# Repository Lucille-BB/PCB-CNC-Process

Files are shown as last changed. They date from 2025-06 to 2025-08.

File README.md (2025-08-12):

# PCB Creation - 3018 Genmitsu CNC

## Purpose
This is documentation from UW-Milwaukee - Center for Sustainable Electrical Energy Systems (SEES) and Microgrid Storage - in order to provide a (somewhat) step by step process for making in house PCB's. 

The PCB in this documentation is very simple. We are integrating NI Modules into the cabinets that control the Microgrid, that read current and voltage sensors. All the PCB is doing is running the NI module and sensor on one end across a 100* ohm resistor, and into two 15 VDC converters. So, we have 20 2-pin connectors and 10 resistors. 

Moreover, I will be providing some of the errors I made in this process to avoid repetitive mistakes, design errors, and unusable boards. Expect to make multiple iterations or redo some parts. I have had to go back and forth in the design process many times to understand the machine and the software. 

## Version History
Similar to the [Severson Group](https://github.com/Severson-Group), the Altium Files for this PCB are saved in this repository as **Vermmddyyyy**

## Software
-------

## Process
* [Altium](./altium.md)
* [FlatCam](./flatcam.md)
* [Candle](./Grbl_candle.md)
* [Outside Resources](./resourcesandlinks.md)

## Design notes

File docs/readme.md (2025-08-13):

# PCB Creation - 3018 Genmitsu CNC

## Purpose
This is documentation from UW-Milwaukee - Center for Sustainable Electrical Energy Systems (SEES) and Microgrid Storage - in order to provide a (somewhat) step by step process for making in house PCB's. 

The PCB in this documentation is very simple. We are integrating NI Modules into the cabinets that control the Microgrid, that read current and voltage sensors. All the PCB is doing is running the NI module and sensor on one end across a 100* ohm resistor, and into two 15 VDC converters. So, we have 20 2-pin connectors and 10 resistors. 

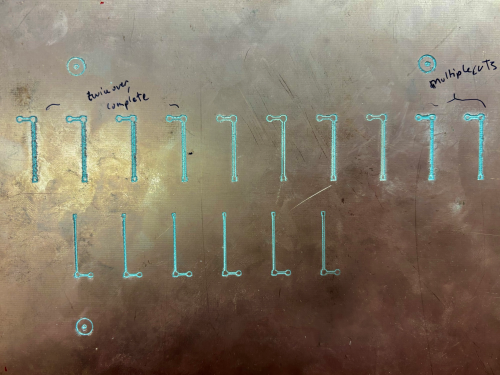
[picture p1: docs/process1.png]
[]()
> above: test board with too thin traces and uneven depth

Moreover, I will be providing some of the errors I made in this process to avoid repetitive mistakes, design errors, and unusable boards. Expect to make multiple iterations or redo some parts. I have had to go back and forth in the design process many times to understand the machine and the software. 

## Process
* [Altium](./altium.md)
* [FlatCam](./flatcam.md)
* [Candle](./grbl_candle.md)
* [Outside Resources](./resourcesandlinks.md)

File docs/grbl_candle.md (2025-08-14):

## Grbl_Candle & Carving 

> [!NOTE]
> Pay close attention to each step you take. It's easy to make little mistakes that un-zero the board. 

### Setting up before Setting Up
Before you begin, watch [this video](https://www.youtube.com/watch?v=u4Mcjz7IP10&t=16s) - particularly the z probe and x-y calibration - to create some helpful settings in Candle for the machine. It is also linked in other resources.
<details>

<summary>My Candle Settings</summary>

> The yellow sections aren't specific to the machine I'm using, and can be directly copy pasted.
> The pink section is the measurement of the z-probe - I used a set of calipers to get an accurate measurement in milimeters, and put that into these settings.
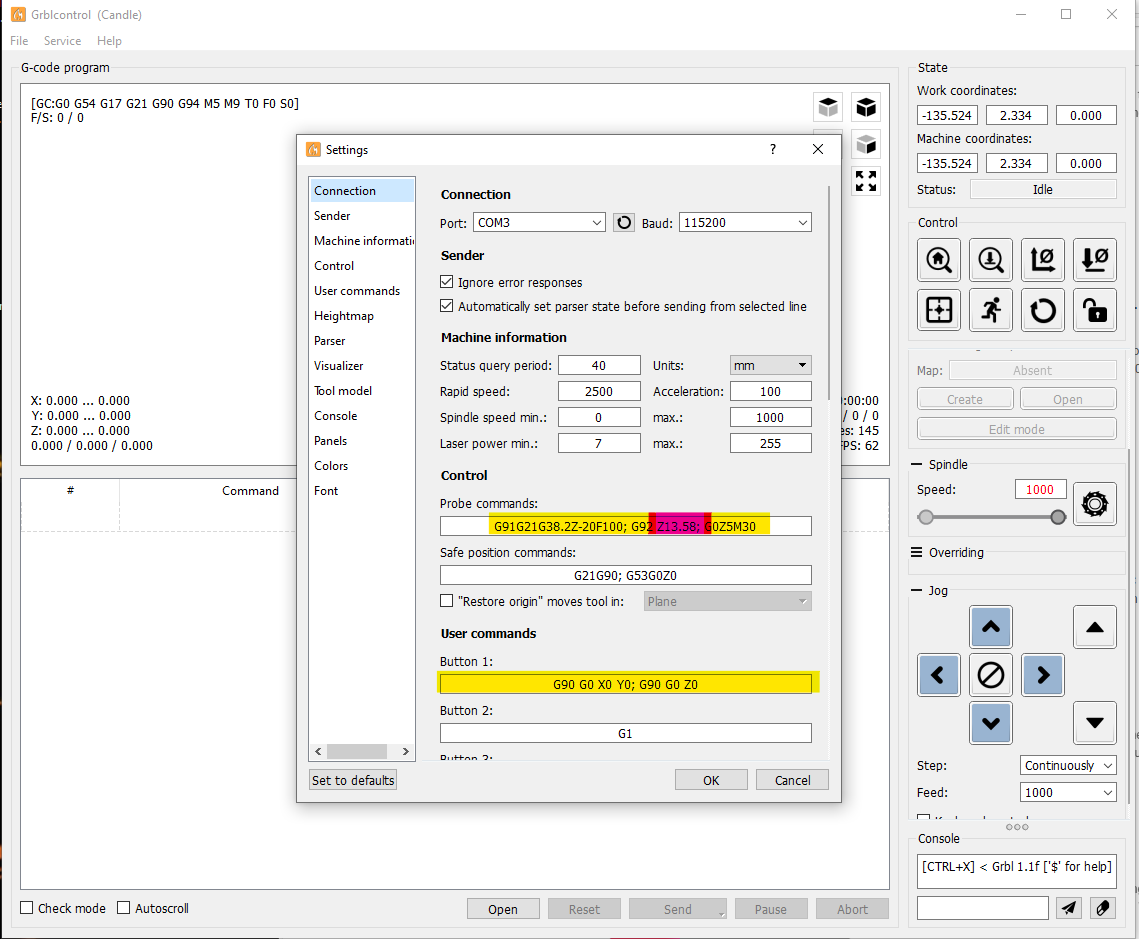
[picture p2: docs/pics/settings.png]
 

</details>

### Setting up

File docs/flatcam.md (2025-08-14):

# FlatCAM

## Opening your files
First, go to File>Open>Open Gerber... and find the Gerber X2 File saved from Altium. You should only need Copper Signal 1 (and 2 if you have a bottom layer), and Profile. Then to open the drill file, repeat the last step, except click on Excellon... and choose filename.TXT. 

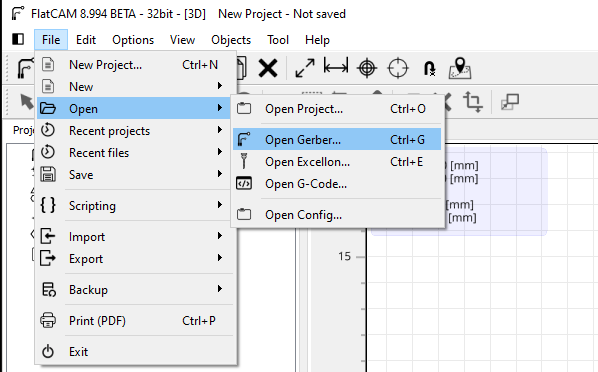
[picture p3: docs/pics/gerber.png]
[]()
> above: here is what your files should look like

If you need to change your x-y axis, select all of your files, then choose Options>Object Transform and adjust the Offset values to adjust where the files are in relation to the axis. I used the offset to place the inner green corner on the axis, instead of the outer green corner. 

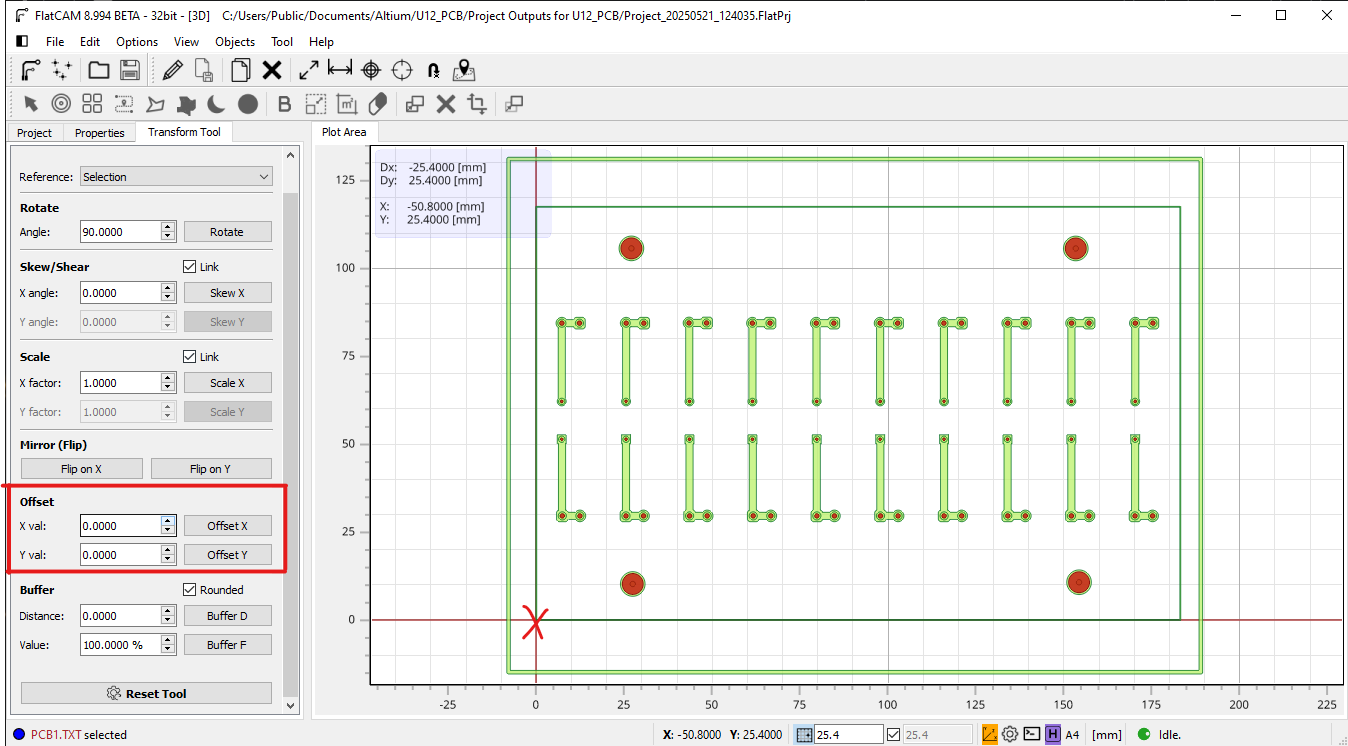
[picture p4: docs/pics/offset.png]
[]()

## Creating the Routing files
Go to Copper Signal 1 (or at least the file with your main traces) and click on Isolation Routing

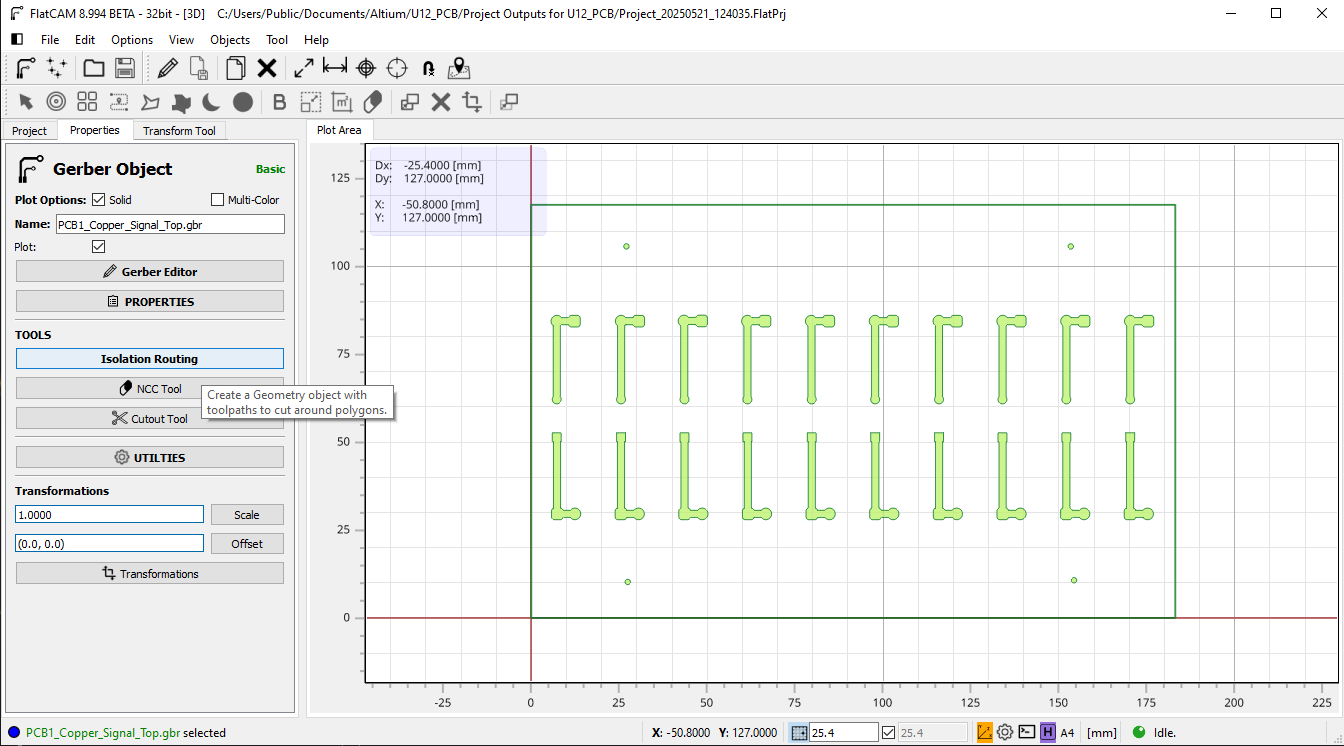
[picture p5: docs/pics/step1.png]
[]()

A sidebar opens up with different options and this will create the "geometry" of your board. This is the in between from the Altium Gerber to the CNC files
* Tool Diameter: Mattwach has a better description for this, but choosing the V tool (even though the standard blades are V) causes problems, and you can't choose the depth the machine cuts, **at least with my version of FlatCAM.** I had so many problems, so I finally just went with C1 (i'm not sure about the others, they might be fine - I haven't played around with that setting exactly). Choose the diameter that you want the final cuts to be - I usually go with 0.3mm which gives plenty of clearance from the rest of the board. If you have a ground plane, this is where it becomes a problem. Despite choosing a 0.3mm wide cut, the ground plane can make this smaller, and not allow your cut outside a certain range. You can change clearance in Altium between a plane and traces, but expect to go through multiple iterations with Altium and CNC-ing the board. 
* Passes: This is how many times the router passes through. I generally go with 3 or 4 to make sure that I get the clearance I want and all the copper removed. 
* Overlap: A higher overlap will overlap the cuts more and also ensure no copper is left behind - set this to 20 - 25% when doing multiple passes.
* Generate Geometry: When you're done, click generate geometry, and it will create filename.grbr_iso_combined 
  
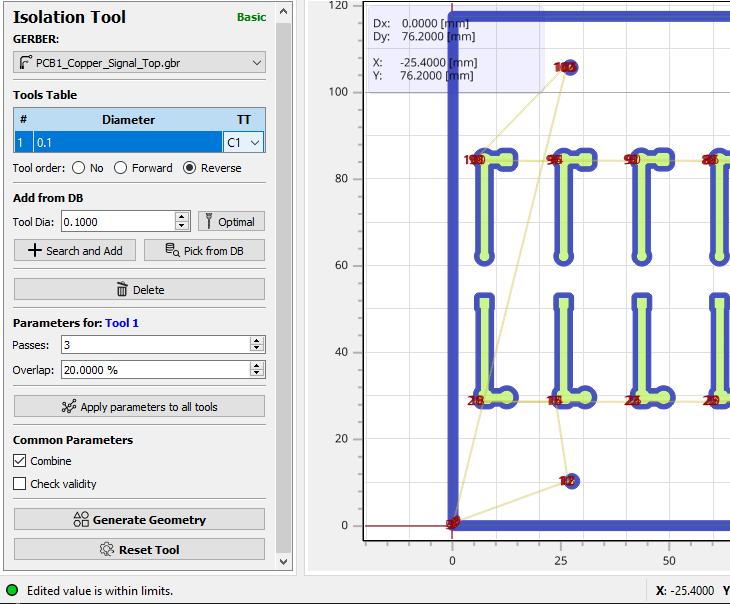
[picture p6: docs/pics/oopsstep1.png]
[]()

From there, we create the actual CNC file. *Ignore some of the parameters set in the picture shown, this is an older file I'm using for an example*
* Cut: Set this as 0.05mm. Ideally you won't need to go any deeper, but I've had times where the heightmap was innaccurate and the copper isn't being carved away. *Generally a range of .05 to 0.15mm is normal. Any deeper and you most likely have a heightmap and bowing issue with the copper. This is a large PCB so there is naturally more variation in the levels of the copper, and air pockets sometimes form between the cutting board and copper.*
* Travel Z: It's good to set this a little lower, around 2 to 5mm. Too low, and you could hit the copper below on accident, and if it's too high, the carving takes longer. 
* Feed rate XY: This can be set around 120 - 240 mm/min. By going with a slower cut rate, breaks in your blade are less likely. However, going 120 is overkill, as it just takes too long for the whole board to be cut out.
* Feed Rate Z: Keep this at about 60 mm/min, this will keep the blade from snapping immediately as it starts carving.
* Spindle Speed: Put this at 10000, because the 3018 is a cheaper machine, the speed isn't exact. Trust that it's very fast and that it works for this process. 

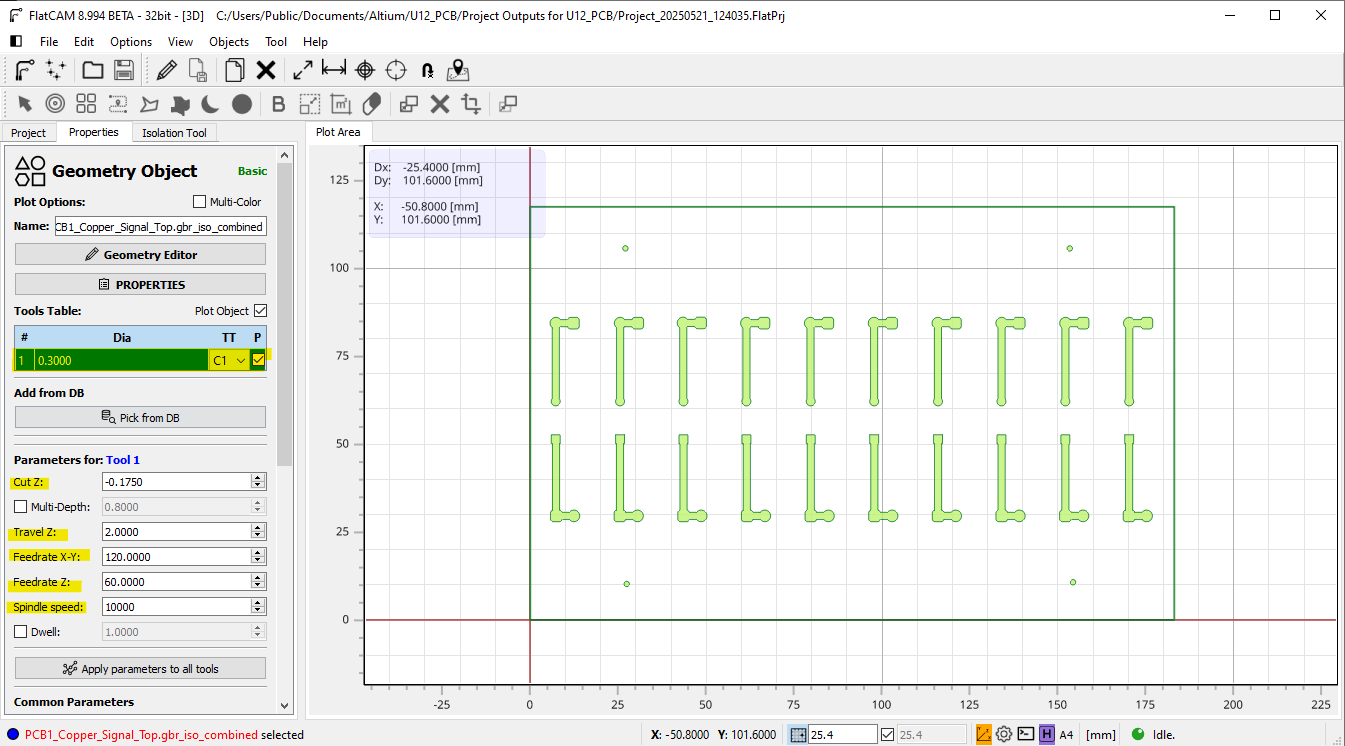
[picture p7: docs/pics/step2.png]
[]()

Finally, on the same panel, scroll down, and you'll see some options
* End Move Z: I set this at 10 cm, which gives enough room for me to access the spindle, without setting the bounds too high for the CNC machine to trip it's limits.
* End move XY: I set this to 0,0 so I can access the spindle to change the blade to a drill and vice versa. This is another measure to make sure the machine is oriented correctly.
Generate the CNC job and you have you routing file all done!
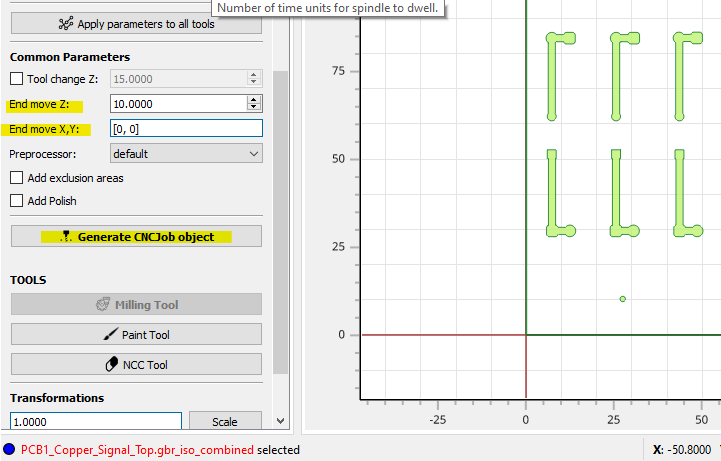
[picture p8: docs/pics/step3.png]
[]()

> [!TIP]
> Come up with a naming system! I made so many different versions of my FlatCam routing files, so come up with a naming system for each. If I changed something fundamentally different in Altium, and went back to FlatCam, I changed the letter from A to B, B to C, etc. If I was changing something small, like the depth of a cut, I'd name them A01, A02, etc. 

## Creating the Drill Files
First, open your filename.TXT file, and choose the highlighted button below

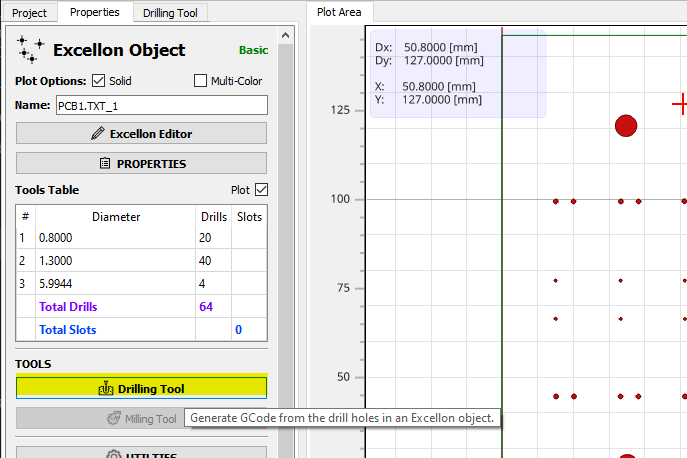
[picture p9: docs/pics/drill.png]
[]()

Similar to Isolation Routing, here are some options on this side panel, and the important ones are highlighted and explained
* Tool Order: Pick Forward or Reverse tool order to make tool changes predictable. You'll be able to see in Candle what the machine is "expecting" to drill next so it's easy to keep track of.
* Cut Z: In order to ensure that your board isn't only halfway cut through, choose around 1.7 to 2mm deep cuts.
* Travel Z: Same as before, aroun d 2mm to 5mm above the board
* Feedrate Z: The endmill/drill bits are able to handle a lot more strain, so 300mm/min has been fine in the past
* Spindle Speed: Set this to 10000, same as before
  
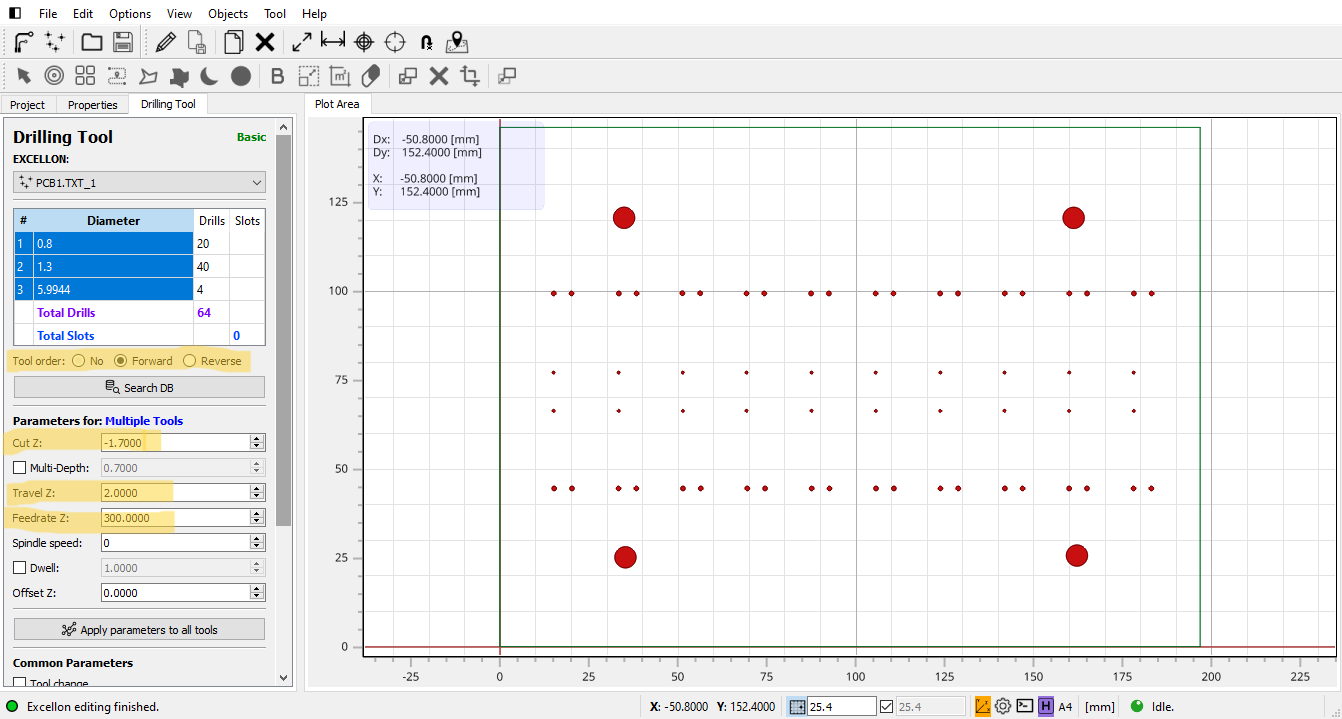
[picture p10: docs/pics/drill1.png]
[]()

**Ignore the settings I have on this file, it's an old one**
* Tool Change Button: Make sure to click on that button so the machine knows to stop before cutting different sized holes
* Tool Change Z: Set this to 10 - 15 cm, so you can easily unscrew and change the bit on the spindle
* End Move Z: Set this where it makes sense. If you need to endmill and cut out a whole piece of copper, it may be a good idea to set this higher to change your bit. Otherwise, it doesn't matter so I set it lower than Tool Change Z.
* End Move X,Y: Set this to 0,0 to make changing the bit easier
* **Preprocessor**: Some tutorials advise using a different preprocessor, or people make their own. It depends on what you need as the user.
  
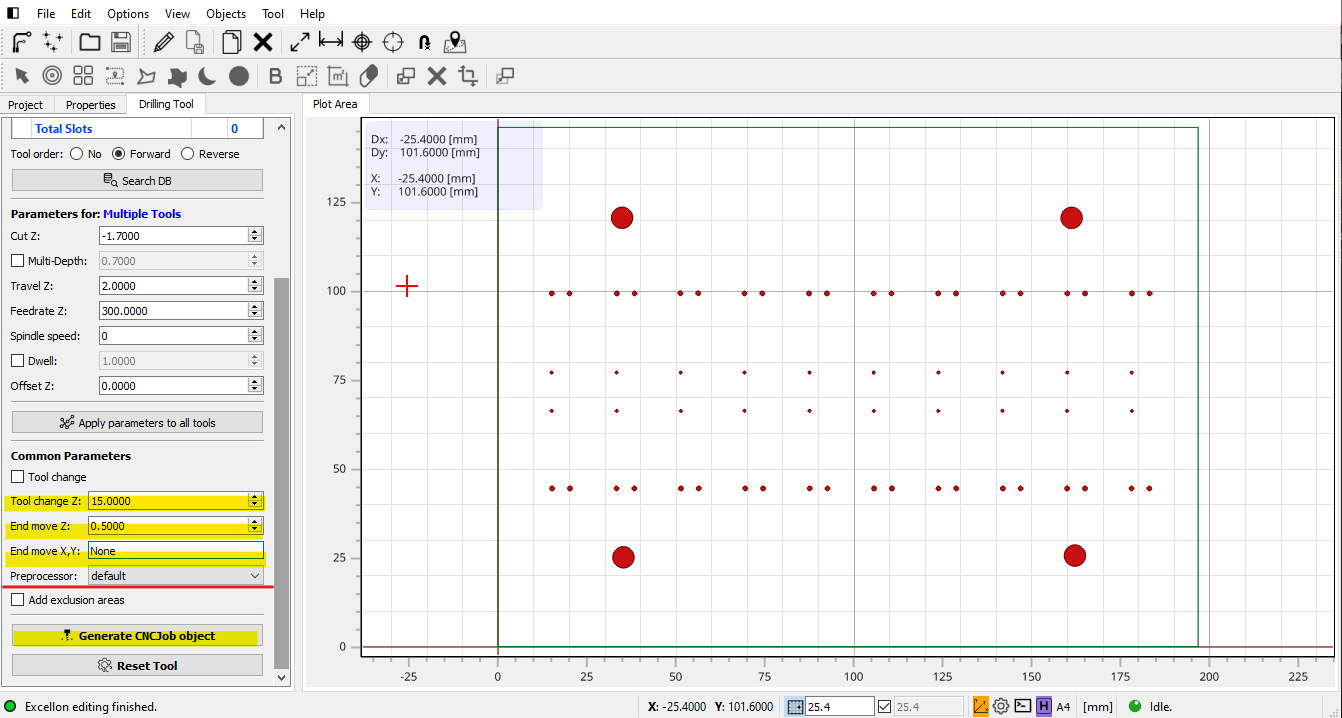
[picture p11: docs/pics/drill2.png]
[]()

## Process
* [Altium](./altium.md)
* [FlatCam](./flatcam.md)
* [Candle](./grbl_candle.md)
* [Outside Resources](./resourcesandlinks.md)

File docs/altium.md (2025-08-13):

# Altium - Designing with the CNC in mind
**I am not doing a full altium "how to" tutorial, however there are some things to keep in mind**

## Schematic 
### OverView: 
Creating the schematic is simple and not much needs to be taken into consideration for later steps. If this process isn't familiar to you, there are plenty of tutorials out there. Altium has decent videos for the design process.

Tips:
* Label nets as much as possible - I did not do this for my first PCB and while it wasn't debilitating, keep it in mind for more complicated boards.
* Use specific components, and not the generic Altium components - the generic ones can create problems when updating to the PCB doc and in the BOM.
* When finding components, its possible the one you want to use isn't in the PCB library. Refer to the [Outside Resources](./resourcesandlinks.md) page for more. 

## PCB Doc 
### OverView:
The PCB Doc is where layout and traces are created, which means that this has more effect on your final product. Sizing is very important and varies from if you are just ordering off of PCB Way. By using the 3018, there is more variation in cut sizes, so we want to make sure the traces actually exist in the final product. 

Tips
* TRACK WIDTH: Go to Design>Rules...>Routing>Width and make the traces about 50 - 70 mils wide (this is pretty wide for most PCB's, if you can go a little smaller without losing the traces, go for it) - therefore the traces won't dissapear once the CNC carves into the copper.
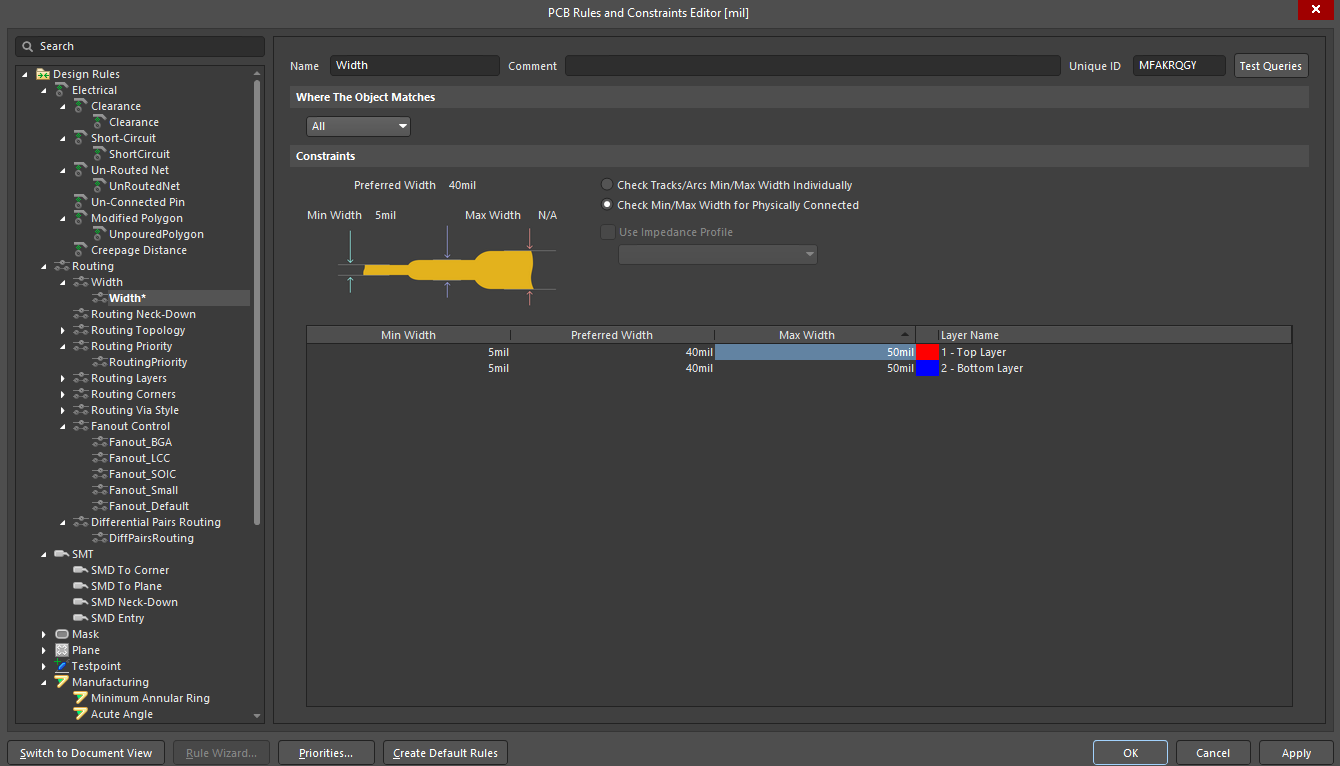
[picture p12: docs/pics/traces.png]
[]()
> above: this is where you can change the design rules. Again, these are ridiculous widths for a normal PCB but the 3018 can be finnicky with smaller traces
* PAD SIZE: This is a lot slower and more manual. To make the process a little easier, go to PCB Filter, and type in "IsPad" and "InAnyComponent". This allows you to only click on the pads and only the pads. Make sure the pads are visibly larger than the traces. By doing so, the CNC will leave enough room for soldering and drilling the holes.
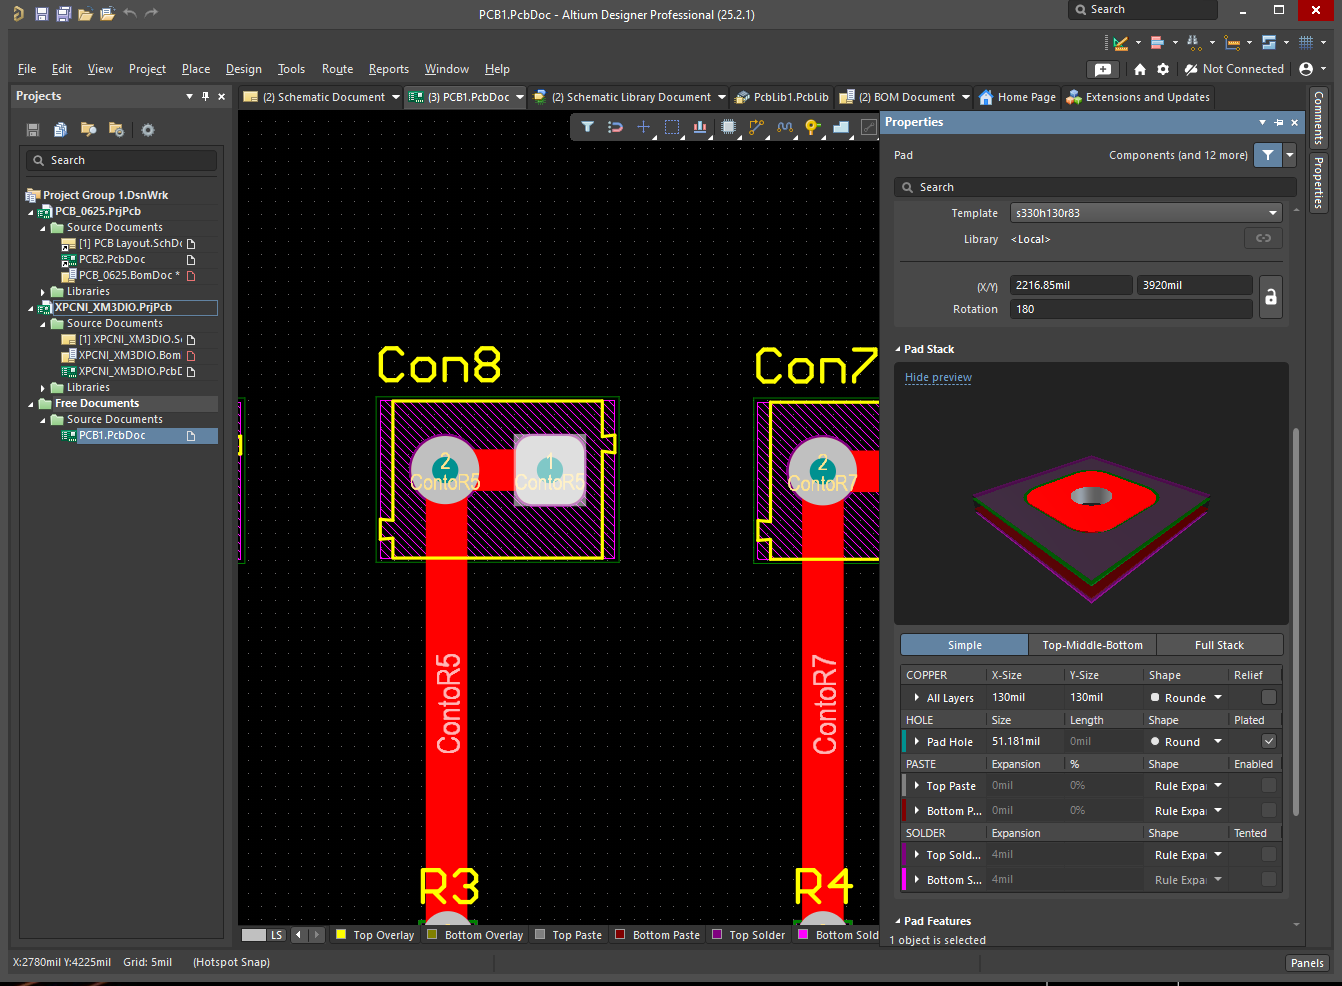
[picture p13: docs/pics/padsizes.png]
[]()
> above: side panel showing pad size in mils
* GROUND PLANE: This board was so simple, it didn't need a ground plane exactly. However, using the 'line' tool will create separation from the rest of the board by removing copper in the CNC process. Adding the ground plane can create complications if you need more seperation from traces and the rest of the board. If a ground plane is needed, go to Design>Rules...>Clearance and go to "Advanced". A table pops up and change the Copper row to adjust clearance between tracks, pads etc. from the copper plane. You can play around with this and adjust as fit. 

## Transferring to FlatCAM
### OverView:
To move from Altium to FlatCAM, you need to export your board. To do so, go to File>Fabrication Outputs> and a sidebar should pop up. You will want to create "Gerber X2 Files" for the pads and traces, and "NC Drill Files" for the component holes. Save and number these as you so choose. I've had to go back and forth from candle to Altium to change the PCB layout and sizings, so numbering is important so you know what version you're using.

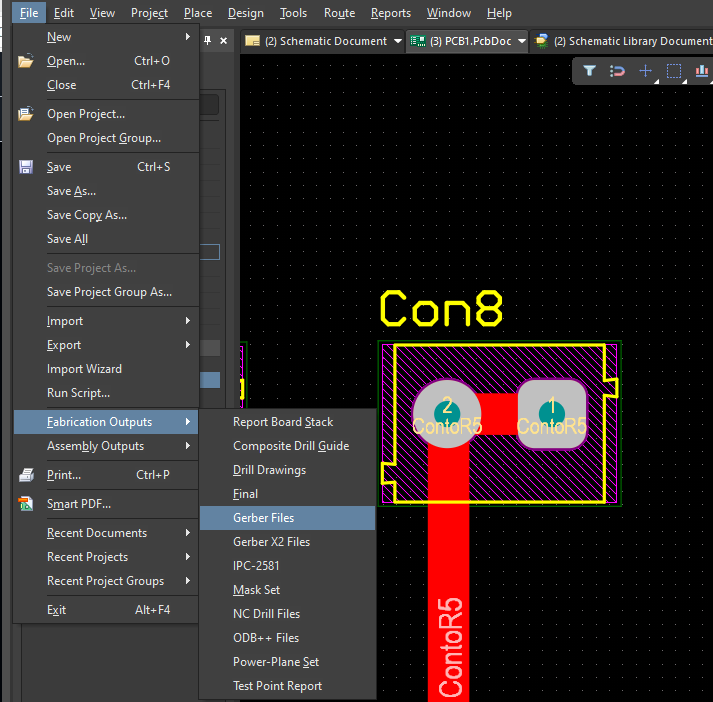
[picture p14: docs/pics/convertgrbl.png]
[]()

## Process
* [Altium](./altium.md)
* [FlatCam](./flatcam.md)
* [Candle](./grbl_candle.md)
* [Outside Resources](./resourcesandlinks.md)

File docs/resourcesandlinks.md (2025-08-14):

## Here I'm compiling many of the videos and readme's that helped me along the way

### The best readME in the universe for 3-d cnc-machining
* [ReadME by mattwach](https://github.com/mattwach/cnc_pcb_tools?tab=readme-ov-file)

### Altium Basics
* Website: [Altium Beginner Documentation](https://www.altium.com/documentation/altium-designer/tutorial-complete-design-walkthrough)
* Video: [Net Labels](https://www.youtube.com/watch?v=HaL3MAUx6Lw)
* Video: [Component Libraries](https://www.youtube.com/watch?v=6h-Z_NJibI8&t=234s)
* Video: [Component Importing](https://www.youtube.com/watch?v=LmAzsCiBLCs)
* *Just pray you don't need to import 3-d component files - follow the ones above and there's plenty for each issue you'll have along they way on YouTube*

### CNC Machining and Set Up
* Video: [Calibrating the CNC Machine](https://www.youtube.com/watch?v=u4Mcjz7IP10&t=16s)

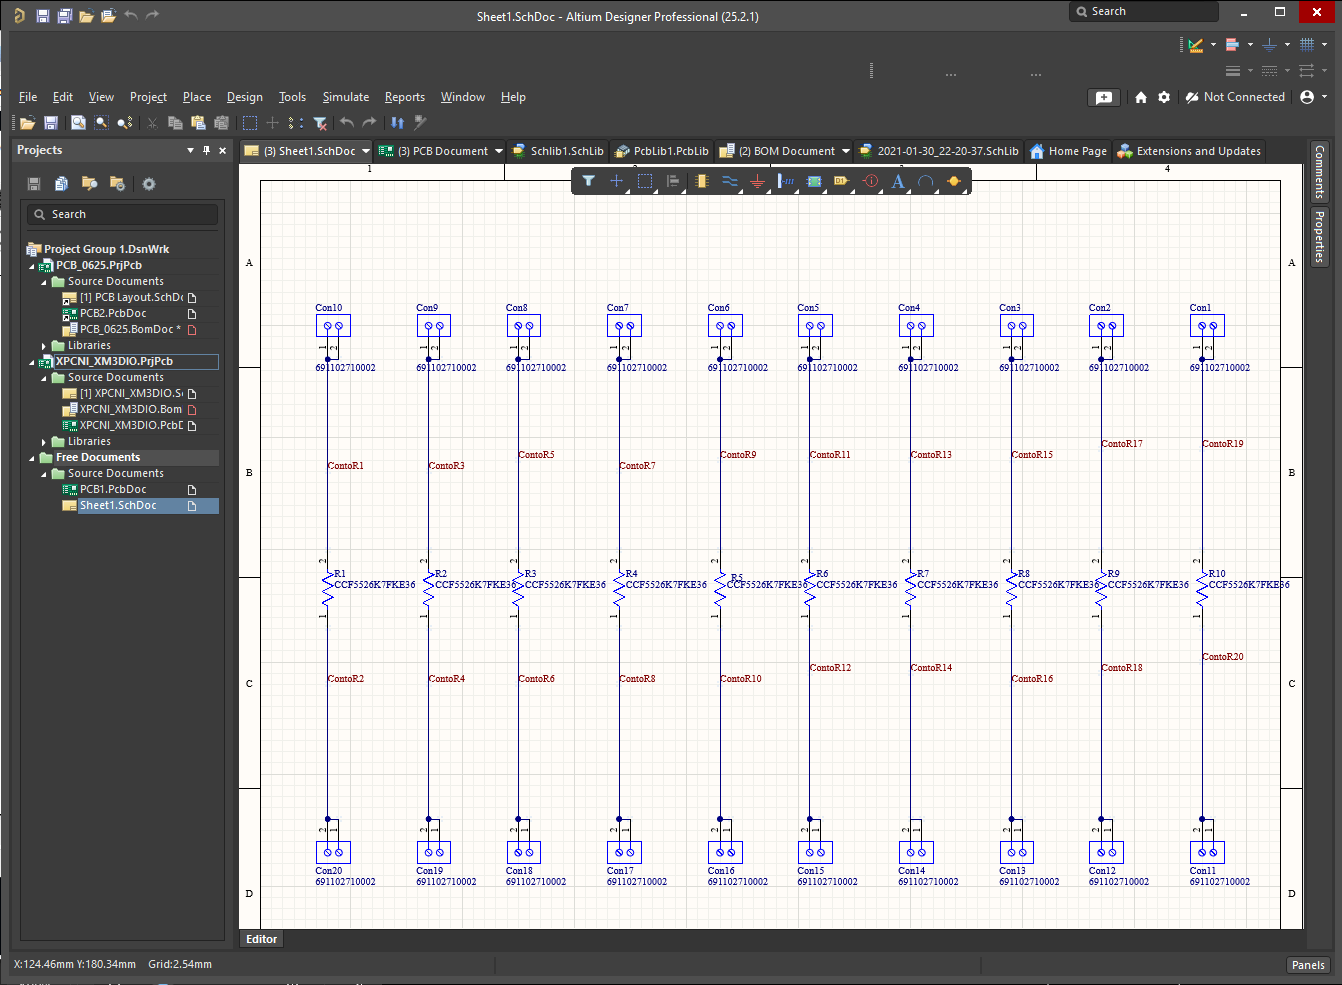
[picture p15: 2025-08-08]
docs/pics/schematic.png

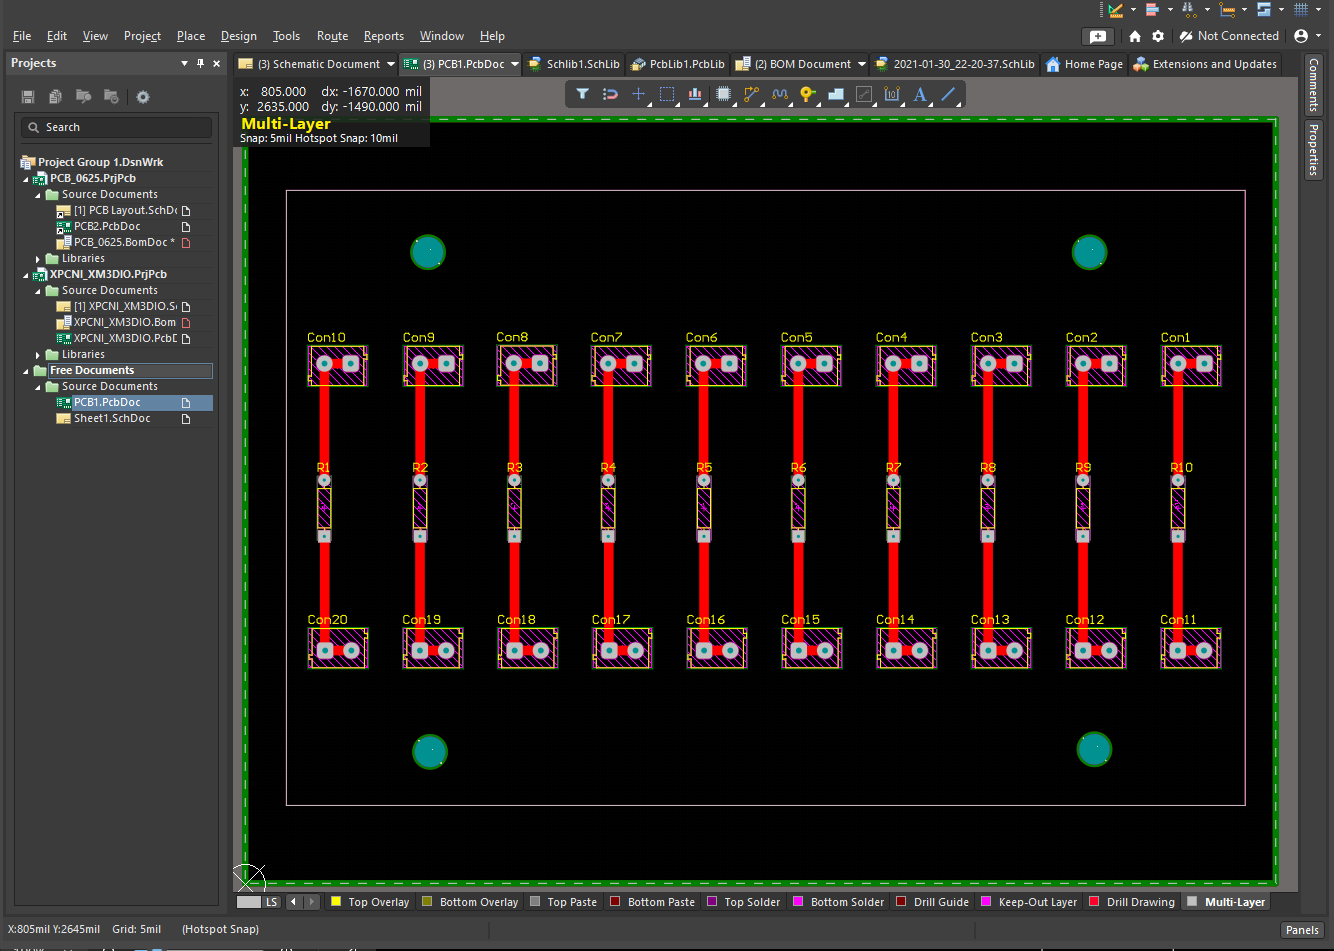
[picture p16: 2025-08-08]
docs/pics/3dpcb.png
